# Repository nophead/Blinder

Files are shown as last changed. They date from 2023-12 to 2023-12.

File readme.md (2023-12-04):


# Blinder

Tasmota roller blind open / close mechanism

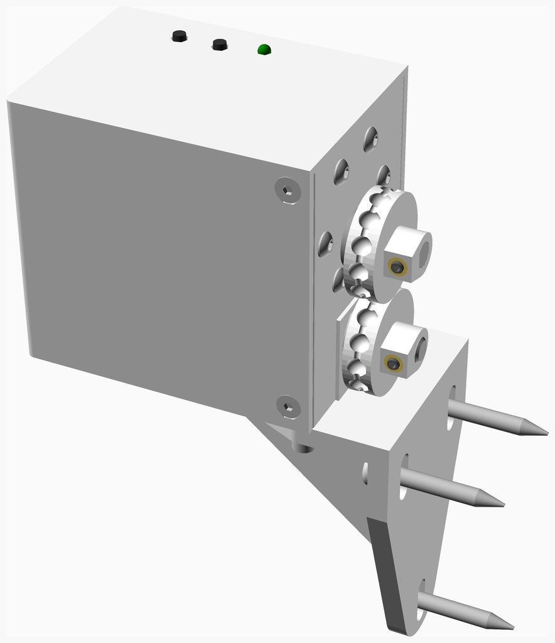
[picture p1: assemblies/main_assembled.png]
Main Assembly


<span></span>

---
## Table of Contents
1. [Parts list](#Parts_list)
1. [Pulley Assembly](#pulley_assembly)
1. [Switch Slide Assembly](#switch_slide_assembly)
1. [Rod Assembly](#rod_assembly)
1. [Retainer Assembly](#retainer_assembly)
1. [Idler Assembly](#idler_assembly)
1. [Base Assembly](#base_assembly)
1. [Motor Assembly](#motor_assembly)
1. [Bracket Assembly](#bracket_assembly)
1. [Blinder PCB Assembly](#blinder_PCB_assembly)
1. [Cover Assembly](#cover_assembly)
1. [Main Assembly](#main_assembly)

<span></span>
[Top](#TOP)

---

## Parts list
| <span style="writing-mode: vertical-rl; text-orientation: mixed;">Switch&nbsp;Slide</span> | <span style="writing-mode: vertical-rl; text-orientation: mixed;">Rod</span> | <span style="writing-mode: vertical-rl; text-orientation: mixed;">Base</span> | <span style="writing-mode: vertical-rl; text-orientation: mixed;">Motor</span> | <span style="writing-mode: vertical-rl; text-orientation: mixed;">Bracket</span> | <span style="writing-mode: vertical-rl; text-orientation: mixed;">Blinder&nbsp;PCB</span> | <span style="writing-mode: vertical-rl; text-orientation: mixed;">Cover</span> | <span style="writing-mode: vertical-rl; text-orientation: mixed;">Main</span> | <span style="writing-mode: vertical-rl; text-orientation: mixed;">TOTALS</span> |  |
|---:|---:|---:|---:|---:|---:|---:|---:|---:|:---|
|  |  |  |  |  |  |  |  | | **Vitamins** |
| &nbsp;&nbsp;.&nbsp; | &nbsp;&nbsp;.&nbsp; | &nbsp;&nbsp;2&nbsp; | &nbsp;&nbsp;.&nbsp; | &nbsp;&nbsp;.&nbsp; | &nbsp;&nbsp;.&nbsp; | &nbsp;&nbsp;.&nbsp; | &nbsp;&nbsp;.&nbsp; |  &nbsp;&nbsp;2&nbsp; | &nbsp;&nbsp; Ball bearing 686ZZ 6mm x 13mm x 5mm |
| &nbsp;&nbsp;.&nbsp; | &nbsp;&nbsp;.&nbsp; | &nbsp;&nbsp;.&nbsp; | &nbsp;&nbsp;.&nbsp; | &nbsp;&nbsp;.&nbsp; | &nbsp;&nbsp;1&nbsp; | &nbsp;&nbsp;.&nbsp; | &nbsp;&nbsp;.&nbsp; |  &nbsp;&nbsp;1&nbsp; | &nbsp;&nbsp; ESP-12F ESP8266 WiFi module |
| &nbsp;&nbsp;2&nbsp; | &nbsp;&nbsp;.&nbsp; | &nbsp;&nbsp;2&nbsp; | &nbsp;&nbsp;.&nbsp; | &nbsp;&nbsp;.&nbsp; | &nbsp;&nbsp;.&nbsp; | &nbsp;&nbsp;.&nbsp; | &nbsp;&nbsp;.&nbsp; |  &nbsp;&nbsp;4&nbsp; | &nbsp;&nbsp; Heatfit insert M2 x 4mm |
| &nbsp;&nbsp;.&nbsp; | &nbsp;&nbsp;.&nbsp; | &nbsp;&nbsp;10&nbsp; | &nbsp;&nbsp;1&nbsp; | &nbsp;&nbsp;.&nbsp; | &nbsp;&nbsp;.&nbsp; | &nbsp;&nbsp;.&nbsp; | &nbsp;&nbsp;.&nbsp; |  &nbsp;&nbsp;11&nbsp; | &nbsp;&nbsp; Heatfit insert M3 x 3mm |
| &nbsp;&nbsp;.&nbsp; | &nbsp;&nbsp;.&nbsp; | &nbsp;&nbsp;.&nbsp; | &nbsp;&nbsp;.&nbsp; | &nbsp;&nbsp;.&nbsp; | &nbsp;&nbsp;1&nbsp; | &nbsp;&nbsp;.&nbsp; | &nbsp;&nbsp;.&nbsp; |  &nbsp;&nbsp;1&nbsp; | &nbsp;&nbsp; JST PH connector 2 way |
| &nbsp;&nbsp;.&nbsp; | &nbsp;&nbsp;.&nbsp; | &nbsp;&nbsp;.&nbsp; | &nbsp;&nbsp;.&nbsp; | &nbsp;&nbsp;.&nbsp; | &nbsp;&nbsp;2&nbsp; | &nbsp;&nbsp;.&nbsp; | &nbsp;&nbsp;.&nbsp; |  &nbsp;&nbsp;2&nbsp; | &nbsp;&nbsp; JST PH connector 3 way |
| &nbsp;&nbsp;.&nbsp; | &nbsp;&nbsp;.&nbsp; | &nbsp;&nbsp;.&nbsp; | &nbsp;&nbsp;.&nbsp; | &nbsp;&nbsp;.&nbsp; | &nbsp;&nbsp;1&nbsp; | &nbsp;&nbsp;.&nbsp; | &nbsp;&nbsp;.&nbsp; |  &nbsp;&nbsp;1&nbsp; | &nbsp;&nbsp; LED 3 mm green |
| &nbsp;&nbsp;.&nbsp; | &nbsp;&nbsp;.&nbsp; | &nbsp;&nbsp;.&nbsp; | &nbsp;&nbsp;.&nbsp; | &nbsp;&nbsp;.&nbsp; | &nbsp;&nbsp;1&nbsp; | &nbsp;&nbsp;.&nbsp; | &nbsp;&nbsp;.&nbsp; |  &nbsp;&nbsp;1&nbsp; | &nbsp;&nbsp; MULTIWATT11 L6203 |
| &nbsp;&nbsp;1&nbsp; | &nbsp;&nbsp;.&nbsp; | &nbsp;&nbsp;1&nbsp; | &nbsp;&nbsp;.&nbsp; | &nbsp;&nbsp;.&nbsp; | &nbsp;&nbsp;.&nbsp; | &nbsp;&nbsp;.&nbsp; | &nbsp;&nbsp;.&nbsp; |  &nbsp;&nbsp;2&nbsp; | &nbsp;&nbsp; Microswitch DM1-00P-110-3 |
| &nbsp;&nbsp;.&nbsp; | &nbsp;&nbsp;.&nbsp; | &nbsp;&nbsp;.&nbsp; | &nbsp;&nbsp;.&nbsp; | &nbsp;&nbsp;.&nbsp; | &nbsp;&nbsp;1&nbsp; | &nbsp;&nbsp;.&nbsp; | &nbsp;&nbsp;.&nbsp; |  &nbsp;&nbsp;1&nbsp; | &nbsp;&nbsp; Molex KK header 2 way |
| &nbsp;&nbsp;.&nbsp; | &nbsp;&nbsp;.&nbsp; | &nbsp;&nbsp;.&nbsp; | &nbsp;&nbsp;.&nbsp; | &nbsp;&nbsp;.&nbsp; | &nbsp;&nbsp;1&nbsp; | &nbsp;&nbsp;.&nbsp; | &nbsp;&nbsp;.&nbsp; |  &nbsp;&nbsp;1&nbsp; | &nbsp;&nbsp; Molex KK housing 2 way |
| &nbsp;&nbsp;.&nbsp; | &nbsp;&nbsp;.&nbsp; | &nbsp;&nbsp;.&nbsp; | &nbsp;&nbsp;.&nbsp; | &nbsp;&nbsp;.&nbsp; | &nbsp;&nbsp;.&nbsp; | &nbsp;&nbsp;1&nbsp; | &nbsp;&nbsp;.&nbsp; |  &nbsp;&nbsp;1&nbsp; | &nbsp;&nbsp; Nut M3 x 2.4mm nyloc |
| &nbsp;&nbsp;.&nbsp; | &nbsp;&nbsp;.&nbsp; | &nbsp;&nbsp;1&nbsp; | &nbsp;&nbsp;.&nbsp; | &nbsp;&nbsp;.&nbsp; | &nbsp;&nbsp;.&nbsp; | &nbsp;&nbsp;.&nbsp; | &nbsp;&nbsp;.&nbsp; |  &nbsp;&nbsp;1&nbsp; | &nbsp;&nbsp; Nut M8 x 6.5mm brass |
| &nbsp;&nbsp;.&nbsp; | &nbsp;&nbsp;.&nbsp; | &nbsp;&nbsp;.&nbsp; | &nbsp;&nbsp;.&nbsp; | &nbsp;&nbsp;.&nbsp; | &nbsp;&nbsp;1&nbsp; | &nbsp;&nbsp;.&nbsp; | &nbsp;&nbsp;.&nbsp; |  &nbsp;&nbsp;1&nbsp; | &nbsp;&nbsp; PCB Blinder |
| &nbsp;&nbsp;.&nbsp; | &nbsp;&nbsp;.&nbsp; | &nbsp;&nbsp;.&nbsp; | &nbsp;&nbsp;.&nbsp; | &nbsp;&nbsp;.&nbsp; | &nbsp;&nbsp;2&nbsp; | &nbsp;&nbsp;.&nbsp; | &nbsp;&nbsp;.&nbsp; |  &nbsp;&nbsp;2&nbsp; | &nbsp;&nbsp; SMD capacitor 0805 100n |
| &nbsp;&nbsp;.&nbsp; | &nbsp;&nbsp;.&nbsp; | &nbsp;&nbsp;.&nbsp; | &nbsp;&nbsp;.&nbsp; | &nbsp;&nbsp;.&nbsp; | &nbsp;&nbsp;2&nbsp; | &nbsp;&nbsp;.&nbsp; | &nbsp;&nbsp;.&nbsp; |  &nbsp;&nbsp;2&nbsp; | &nbsp;&nbsp; SMD capacitor 0805 15n |
| &nbsp;&nbsp;.&nbsp; | &nbsp;&nbsp;.&nbsp; | &nbsp;&nbsp;.&nbsp; | &nbsp;&nbsp;.&nbsp; | &nbsp;&nbsp;.&nbsp; | &nbsp;&nbsp;1&nbsp; | &nbsp;&nbsp;.&nbsp; | &nbsp;&nbsp;.&nbsp; |  &nbsp;&nbsp;1&nbsp; | &nbsp;&nbsp; SMD capacitor 0805 220n |
| &nbsp;&nbsp;.&nbsp; | &nbsp;&nbsp;.&nbsp; | &nbsp;&nbsp;.&nbsp; | &nbsp;&nbsp;.&nbsp; | &nbsp;&nbsp;.&nbsp; | &nbsp;&nbsp;5&nbsp; | &nbsp;&nbsp;.&nbsp; | &nbsp;&nbsp;.&nbsp; |  &nbsp;&nbsp;5&nbsp; | &nbsp;&nbsp; SMD resistor 0805 10K 0.125W |
| &nbsp;&nbsp;.&nbsp; | &nbsp;&nbsp;.&nbsp; | &nbsp;&nbsp;.&nbsp; | &nbsp;&nbsp;.&nbsp; | &nbsp;&nbsp;.&nbsp; | &nbsp;&nbsp;2&nbsp; | &nbsp;&nbsp;.&nbsp; | &nbsp;&nbsp;.&nbsp; |  &nbsp;&nbsp;2&nbsp; | &nbsp;&nbsp; SMD resistor 0805 1K 0.125W |
| &nbsp;&nbsp;.&nbsp; | &nbsp;&nbsp;.&nbsp; | &nbsp;&nbsp;.&nbsp; | &nbsp;&nbsp;.&nbsp; | &nbsp;&nbsp;.&nbsp; | &nbsp;&nbsp;1&nbsp; | &nbsp;&nbsp;.&nbsp; | &nbsp;&nbsp;.&nbsp; |  &nbsp;&nbsp;1&nbsp; | &nbsp;&nbsp; SMD resistor 0805 2K2 0.125W |
| &nbsp;&nbsp;2&nbsp; | &nbsp;&nbsp;.&nbsp; | &nbsp;&nbsp;2&nbsp; | &nbsp;&nbsp;.&nbsp; | &nbsp;&nbsp;.&nbsp; | &nbsp;&nbsp;.&nbsp; | &nbsp;&nbsp;.&nbsp; | &nbsp;&nbsp;.&nbsp; |  &nbsp;&nbsp;4&nbsp; | &nbsp;&nbsp; Screw M2 cap x 10mm |
| &nbsp;&nbsp;.&nbsp; | &nbsp;&nbsp;.&nbsp; | &nbsp;&nbsp;1&nbsp; | &nbsp;&nbsp;.&nbsp; | &nbsp;&nbsp;.&nbsp; | &nbsp;&nbsp;.&nbsp; | &nbsp;&nbsp;.&nbsp; | &nbsp;&nbsp;.&nbsp; |  &nbsp;&nbsp;1&nbsp; | &nbsp;&nbsp; Screw M3 cap x  5mm |
| &nbsp;&nbsp;.&nbsp; | &nbsp;&nbsp;.&nbsp; | &nbsp;&nbsp;.&nbsp; | &nbsp;&nbsp;.&nbsp; | &nbsp;&nbsp;3&nbsp; | &nbsp;&nbsp;.&nbsp; | &nbsp;&nbsp;.&nbsp; | &nbsp;&nbsp;.&nbsp; |  &nbsp;&nbsp;3&nbsp; | &nbsp;&nbsp; Screw M3 cap x  8mm |
| &nbsp;&nbsp;.&nbsp; | &nbsp;&nbsp;.&nbsp; | &nbsp;&nbsp;.&nbsp; | &nbsp;&nbsp;.&nbsp; | &nbsp;&nbsp;.&nbsp; | &nbsp;&nbsp;.&nbsp; | &nbsp;&nbsp;.&nbsp; | &nbsp;&nbsp;4&nbsp; |  &nbsp;&nbsp;4&nbsp; | &nbsp;&nbsp; Screw M3 cs cap x  5mm |
| &nbsp;&nbsp;.&nbsp; | &nbsp;&nbsp;.&nbsp; | &nbsp;&nbsp;.&nbsp; | &nbsp;&nbsp;.&nbsp; | &nbsp;&nbsp;.&nbsp; | &nbsp;&nbsp;.&nbsp; | &nbsp;&nbsp;1&nbsp; | &nbsp;&nbsp;.&nbsp; |  &nbsp;&nbsp;1&nbsp; | &nbsp;&nbsp; Screw M3 cs cap x 12mm |
| &nbsp;&nbsp;.&nbsp; | &nbsp;&nbsp;.&nbsp; | &nbsp;&nbsp;.&nbsp; | &nbsp;&nbsp;6&nbsp; | &nbsp;&nbsp;.&nbsp; | &nbsp;&nbsp;.&nbsp; | &nbsp;&nbsp;.&nbsp; | &nbsp;&nbsp;.&nbsp; |  &nbsp;&nbsp;6&nbsp; | &nbsp;&nbsp; Screw M3 dome x 12mm |
| &nbsp;&nbsp;.&nbsp; | &nbsp;&nbsp;.&nbsp; | &nbsp;&nbsp;2&nbsp; | &nbsp;&nbsp;1&nbsp; | &nbsp;&nbsp;.&nbsp; | &nbsp;&nbsp;.&nbsp; | &nbsp;&nbsp;.&nbsp; | &nbsp;&nbsp;.&nbsp; |  &nbsp;&nbsp;3&nbsp; | &nbsp;&nbsp; Screw M3 grub x  5mm |
| &nbsp;&nbsp;.&nbsp; | &nbsp;&nbsp;.&nbsp; | &nbsp;&nbsp;.&nbsp; | &nbsp;&nbsp;.&nbsp; | &nbsp;&nbsp;3&nbsp; | &nbsp;&nbsp;.&nbsp; | &nbsp;&nbsp;.&nbsp; | &nbsp;&nbsp;.&nbsp; |  &nbsp;&nbsp;3&nbsp; | &nbsp;&nbsp; Screw No8 pan wood x 30mm |
| &nbsp;&nbsp;.&nbsp; | &nbsp;&nbsp;.&nbsp; | &nbsp;&nbsp;.&nbsp; | &nbsp;&nbsp;.&nbsp; | &nbsp;&nbsp;.&nbsp; | &nbsp;&nbsp;2&nbsp; | &nbsp;&nbsp;.&nbsp; | &nbsp;&nbsp;.&nbsp; |  &nbsp;&nbsp;2&nbsp; | &nbsp;&nbsp; Square button 6mm |
| &nbsp;&nbsp;.&nbsp; | &nbsp;&nbsp;1&nbsp; | &nbsp;&nbsp;.&nbsp; | &nbsp;&nbsp;.&nbsp; | &nbsp;&nbsp;.&nbsp; | &nbsp;&nbsp;.&nbsp; | &nbsp;&nbsp;.&nbsp; | &nbsp;&nbsp;.&nbsp; |  &nbsp;&nbsp;1&nbsp; | &nbsp;&nbsp; Threaded rod M8 x 79mm - not shown |
| &nbsp;&nbsp;.&nbsp; | &nbsp;&nbsp;.&nbsp; | &nbsp;&nbsp;.&nbsp; | &nbsp;&nbsp;.&nbsp; | &nbsp;&nbsp;.&nbsp; | &nbsp;&nbsp;1&nbsp; | &nbsp;&nbsp;.&nbsp; | &nbsp;&nbsp;.&nbsp; |  &nbsp;&nbsp;1&nbsp; | &nbsp;&nbsp; Ultra Small 3A buck regulator |
| &nbsp;&nbsp;2&nbsp; | &nbsp;&nbsp;.&nbsp; | &nbsp;&nbsp;2&nbsp; | &nbsp;&nbsp;.&nbsp; | &nbsp;&nbsp;.&nbsp; | &nbsp;&nbsp;.&nbsp; | &nbsp;&nbsp;.&nbsp; | &nbsp;&nbsp;.&nbsp; |  &nbsp;&nbsp;4&nbsp; | &nbsp;&nbsp; Washer  M2 x 5mm x 0.3mm |
| &nbsp;&nbsp;.&nbsp; | &nbsp;&nbsp;.&nbsp; | &nbsp;&nbsp;1&nbsp; | &nbsp;&nbsp;.&nbsp; | &nbsp;&nbsp;3&nbsp; | &nbsp;&nbsp;.&nbsp; | &nbsp;&nbsp;1&nbsp; | &nbsp;&nbsp;.&nbsp; |  &nbsp;&nbsp;5&nbsp; | &nbsp;&nbsp; Washer  M3 x 7mm x 0.5mm |
| &nbsp;&nbsp;.&nbsp; | &nbsp;&nbsp;.&nbsp; | &nbsp;&nbsp;.&nbsp; | &nbsp;&nbsp;.&nbsp; | &nbsp;&nbsp;3&nbsp; | &nbsp;&nbsp;.&nbsp; | &nbsp;&nbsp;.&nbsp; | &nbsp;&nbsp;.&nbsp; |  &nbsp;&nbsp;3&nbsp; | &nbsp;&nbsp; Washer  M5 x 10mm x 1mm |
| &nbsp;&nbsp;.&nbsp; | &nbsp;&nbsp;.&nbsp; | &nbsp;&nbsp;2&nbsp; | &nbsp;&nbsp;.&nbsp; | &nbsp;&nbsp;.&nbsp; | &nbsp;&nbsp;.&nbsp; | &nbsp;&nbsp;.&nbsp; | &nbsp;&nbsp;.&nbsp; |  &nbsp;&nbsp;2&nbsp; | &nbsp;&nbsp; Washer spring M6 x 1.9mm |
| &nbsp;&nbsp;2&nbsp; | &nbsp;&nbsp;.&nbsp; | &nbsp;&nbsp;2&nbsp; | &nbsp;&nbsp;.&nbsp; | &nbsp;&nbsp;.&nbsp; | &nbsp;&nbsp;.&nbsp; | &nbsp;&nbsp;.&nbsp; | &nbsp;&nbsp;.&nbsp; |  &nbsp;&nbsp;4&nbsp; | &nbsp;&nbsp; Washer star M2 x 0.3mm |
| &nbsp;&nbsp;.&nbsp; | &nbsp;&nbsp;.&nbsp; | &nbsp;&nbsp;1&nbsp; | &nbsp;&nbsp;.&nbsp; | &nbsp;&nbsp;.&nbsp; | &nbsp;&nbsp;.&nbsp; | &nbsp;&nbsp;.&nbsp; | &nbsp;&nbsp;.&nbsp; |  &nbsp;&nbsp;1&nbsp; | &nbsp;&nbsp; Washer star M3 x 0.5mm |
| &nbsp;&nbsp;9&nbsp; | &nbsp;&nbsp;1&nbsp; | &nbsp;&nbsp;29&nbsp; | &nbsp;&nbsp;8&nbsp; | &nbsp;&nbsp;12&nbsp; | &nbsp;&nbsp;25&nbsp; | &nbsp;&nbsp;3&nbsp; | &nbsp;&nbsp;4&nbsp; | &nbsp;&nbsp;91&nbsp; | &nbsp;&nbsp;Total vitamins count |
|  |  |  |  |  |  |  |  | | **3D printed parts** |
| &nbsp;&nbsp;.&nbsp; | &nbsp;&nbsp;.&nbsp; | &nbsp;&nbsp;1&nbsp; | &nbsp;&nbsp;.&nbsp; | &nbsp;&nbsp;.&nbsp; | &nbsp;&nbsp;.&nbsp; | &nbsp;&nbsp;.&nbsp; | &nbsp;&nbsp;.&nbsp; |  &nbsp;&nbsp;1&nbsp; | &nbsp;&nbsp;base.stl |
| &nbsp;&nbsp;.&nbsp; | &nbsp;&nbsp;.&nbsp; | &nbsp;&nbsp;.&nbsp; | &nbsp;&nbsp;.&nbsp; | &nbsp;&nbsp;1&nbsp; | &nbsp;&nbsp;.&nbsp; | &nbsp;&nbsp;.&nbsp; | &nbsp;&nbsp;.&nbsp; |  &nbsp;&nbsp;1&nbsp; | &nbsp;&nbsp;bracket.stl |
| &nbsp;&nbsp;.&nbsp; | &nbsp;&nbsp;.&nbsp; | &nbsp;&nbsp;.&nbsp; | &nbsp;&nbsp;.&nbsp; | &nbsp;&nbsp;.&nbsp; | &nbsp;&nbsp;.&nbsp; | &nbsp;&nbsp;1&nbsp; | &nbsp;&nbsp;.&nbsp; |  &nbsp;&nbsp;1&nbsp; | &nbsp;&nbsp;cover.stl |
| &nbsp;&nbsp;.&nbsp; | &nbsp;&nbsp;.&nbsp; | &nbsp;&nbsp;1&nbsp; | &nbsp;&nbsp;.&nbsp; | &nbsp;&nbsp;.&nbsp; | &nbsp;&nbsp;.&nbsp; | &nbsp;&nbsp;.&nbsp; | &nbsp;&nbsp;.&nbsp; |  &nbsp;&nbsp;1&nbsp; | &nbsp;&nbsp;idler.stl |
| &nbsp;&nbsp;.&nbsp; | &nbsp;&nbsp;.&nbsp; | &nbsp;&nbsp;.&nbsp; | &nbsp;&nbsp;1&nbsp; | &nbsp;&nbsp;.&nbsp; | &nbsp;&nbsp;.&nbsp; | &nbsp;&nbsp;.&nbsp; | &nbsp;&nbsp;.&nbsp; |  &nbsp;&nbsp;1&nbsp; | &nbsp;&nbsp;pulley.stl |
| &nbsp;&nbsp;.&nbsp; | &nbsp;&nbsp;.&nbsp; | &nbsp;&nbsp;1&nbsp; | &nbsp;&nbsp;.&nbsp; | &nbsp;&nbsp;.&nbsp; | &nbsp;&nbsp;.&nbsp; | &nbsp;&nbsp;.&nbsp; | &nbsp;&nbsp;.&nbsp; |  &nbsp;&nbsp;1&nbsp; | &nbsp;&nbsp;retainer.stl |
| &nbsp;&nbsp;1&nbsp; | &nbsp;&nbsp;.&nbsp; | &nbsp;&nbsp;.&nbsp; | &nbsp;&nbsp;.&nbsp; | &nbsp;&nbsp;.&nbsp; | &nbsp;&nbsp;.&nbsp; | &nbsp;&nbsp;.&nbsp; | &nbsp;&nbsp;.&nbsp; |  &nbsp;&nbsp;1&nbsp; | &nbsp;&nbsp;switch_slide.stl |
| &nbsp;&nbsp;1&nbsp; | &nbsp;&nbsp;.&nbsp; | &nbsp;&nbsp;3&nbsp; | &nbsp;&nbsp;1&nbsp; | &nbsp;&nbsp;1&nbsp; | &nbsp;&nbsp;.&nbsp; | &nbsp;&nbsp;1&nbsp; | &nbsp;&nbsp;.&nbsp; | &nbsp;&nbsp;7&nbsp; | &nbsp;&nbsp;Total 3D printed parts count |

<span></span>
[Top](#TOP)

---

## Pulley Assembly
### Vitamins
|Qty|Description|
|---:|:---|
|1| Heatfit insert M3 x 3mm|
|1| Screw M3 grub x  5mm|

### 3D Printed parts

| 1 x pulley.stl |
|---|
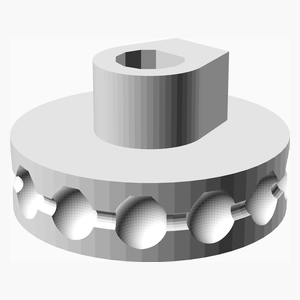
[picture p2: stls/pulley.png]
pulley.stl
|  

### Assembly instructions
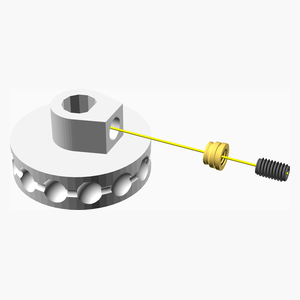
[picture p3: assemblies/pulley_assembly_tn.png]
pulley_assembly


1. Fit the heatfit insert
1. Add the grub screw

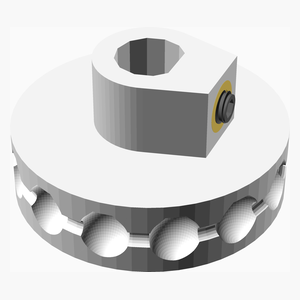
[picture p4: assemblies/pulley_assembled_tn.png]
pulley_assembled


<span></span>
[Top](#TOP)

---

## Switch Slide Assembly
### Vitamins
|Qty|Description|
|---:|:---|
|2| Heatfit insert M2 x 4mm|
|1| Microswitch DM1-00P-110-3|
|2| Screw M2 cap x 10mm|
|2| Washer  M2 x 5mm x 0.3mm|
|2| Washer star M2 x 0.3mm|

### 3D Printed parts

| 1 x switch_slide.stl |
|---|
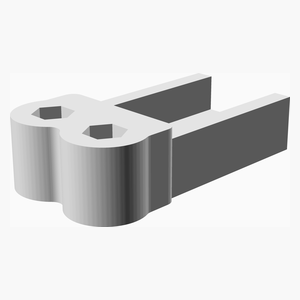
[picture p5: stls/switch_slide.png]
switch_slide.stl
|  

### Assembly instructions
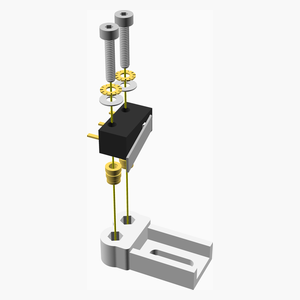
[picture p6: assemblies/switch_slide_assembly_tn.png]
switch_slide_assembly


1. Fit the heatfit inserts into the slide.
1. Screw the microswitch to the slide using 10mm M2 cap screws spring washers and plain washers.
1. Solder two wires to the outer pins.

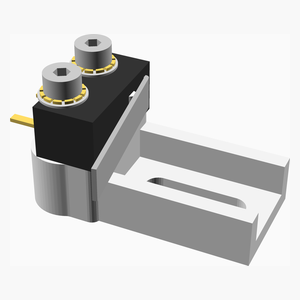
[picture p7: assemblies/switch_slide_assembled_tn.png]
switch_slide_assembled


<span></span>
[Top](#TOP)

---

## Rod Assembly
### Vitamins
|Qty|Description|
|---:|:---|
|1| Threaded rod M8 x 79mm - not shown|

### Assembly instructions
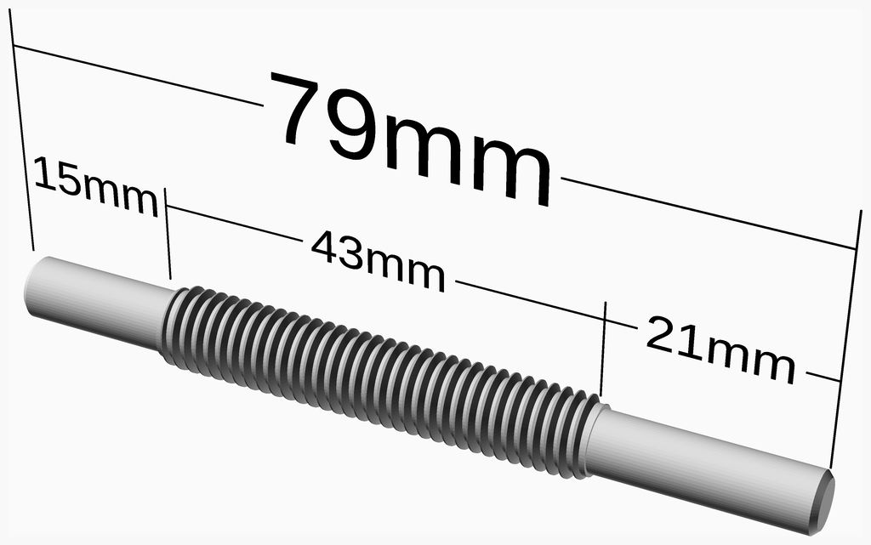
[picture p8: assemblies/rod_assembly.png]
rod_assembly


* Turn down the ends of the studding to 5.96mm to fit through the bearings.

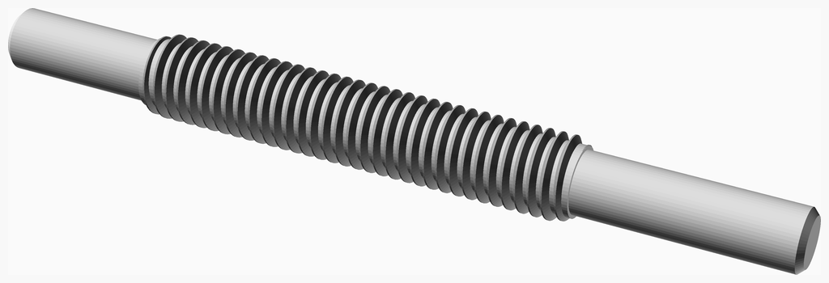
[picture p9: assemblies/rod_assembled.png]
rod_assembled


<span></span>
[Top](#TOP)

---

## Retainer Assembly
### Vitamins
|Qty|Description|
|---:|:---|
|1| Heatfit insert M3 x 3mm|
|1| Screw M3 grub x  5mm|

### 3D Printed parts

| 1 x retainer.stl |
|---|
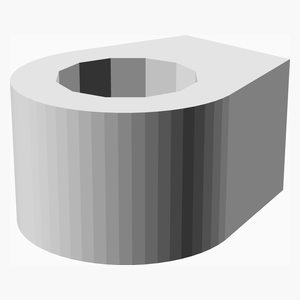
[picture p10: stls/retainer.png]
retainer.stl
|  

### Assembly instructions
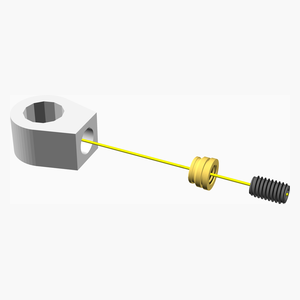
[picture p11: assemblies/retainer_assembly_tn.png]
retainer_assembly


1. Fit the heatfit insert
1. Add the grub screw

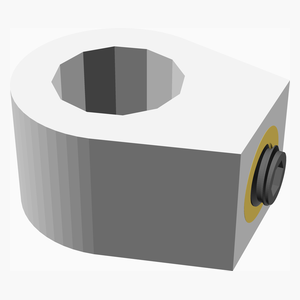
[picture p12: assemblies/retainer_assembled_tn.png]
retainer_assembled


<span></span>
[Top](#TOP)

---

## Idler Assembly
### Vitamins
|Qty|Description|
|---:|:---|
|1| Heatfit insert M3 x 3mm|
|1| Screw M3 grub x  5mm|

### 3D Printed parts

| 1 x idler.stl |
|---|
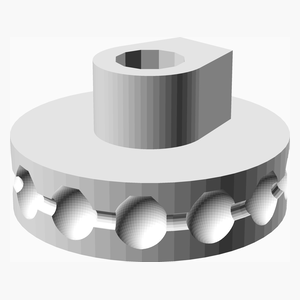
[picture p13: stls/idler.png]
idler.stl
|  

### Assembly instructions
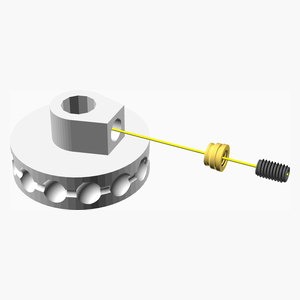
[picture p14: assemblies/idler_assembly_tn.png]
idler_assembly


1. Fit the heatfit insert
1. Add the grub screw

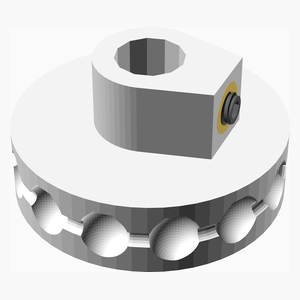
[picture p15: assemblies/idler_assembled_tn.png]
idler_assembled


<span></span>
[Top](#TOP)

---

## Base Assembly
### Vitamins
|Qty|Description|
|---:|:---|
|2| Ball bearing 686ZZ 6mm x 13mm x 5mm|
|2| Heatfit insert M2 x 4mm|
|8| Heatfit insert M3 x 3mm|
|1| Microswitch DM1-00P-110-3|
|1| Nut M8 x 6.5mm brass|
|2| Screw M2 cap x 10mm|
|1| Screw M3 cap x  5mm|
|2| Washer  M2 x 5mm x 0.3mm|
|1| Washer  M3 x 7mm x 0.5mm|
|2| Washer spring M6 x 1.9mm|
|2| Washer star M2 x 0.3mm|
|1| Washer star M3 x 0.5mm|

### 3D Printed parts

| 1 x base.stl |
|---|
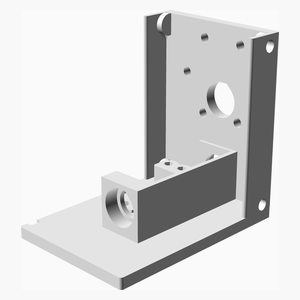
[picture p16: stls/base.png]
base.stl
|  

### Sub-assemblies

| 1 x idler_assembly | 1 x retainer_assembly | 1 x rod_assembly |
|---|---|---|
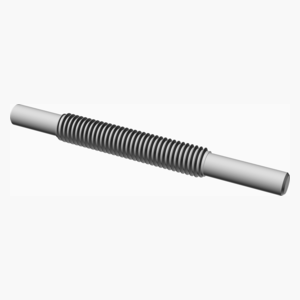
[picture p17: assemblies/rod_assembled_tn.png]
rod_assembled
| idler_assembled | retainer_assembled |  

| 1 x switch_slide_assembly |
|---|
| switch_slide_assembled 

### Assembly instructions
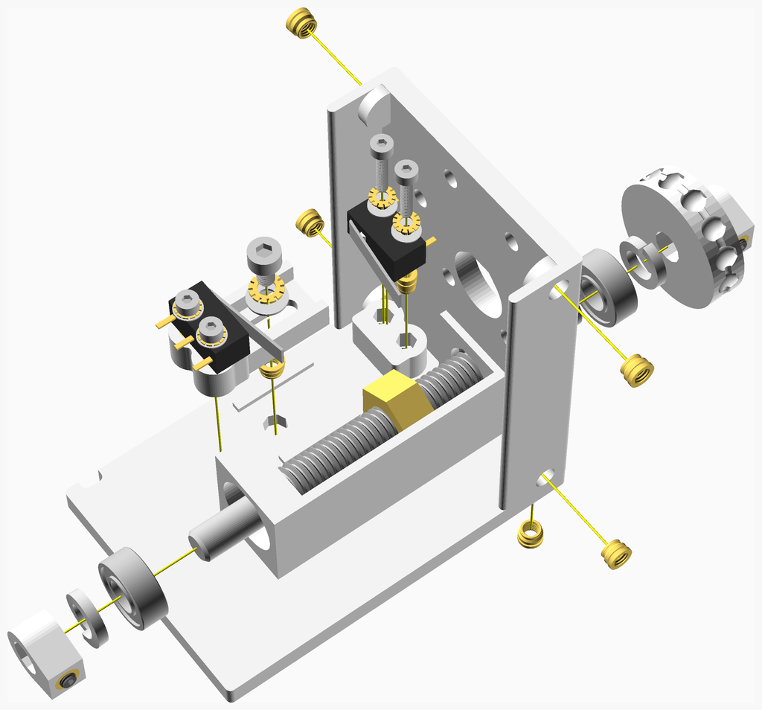
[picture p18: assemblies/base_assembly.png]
base_assembly


1. Fit the 8 M3 inserts, 4 in the ribs, 3 in the base and 1 for the slide
1. Fit two M2 inserts for the microswitch.
1. Place the M8 nut in a central position and screw in the studding.
1. Crush the M8 spring washers with pliers as they are used just as spacers.
1. Fit the bearings and spring washers and secure in place with the pulley and retainer grub screws.
1. Solder two wires to the outer pins of the microswitch and screw it in place.
1. Screw the slide in place in the central position.

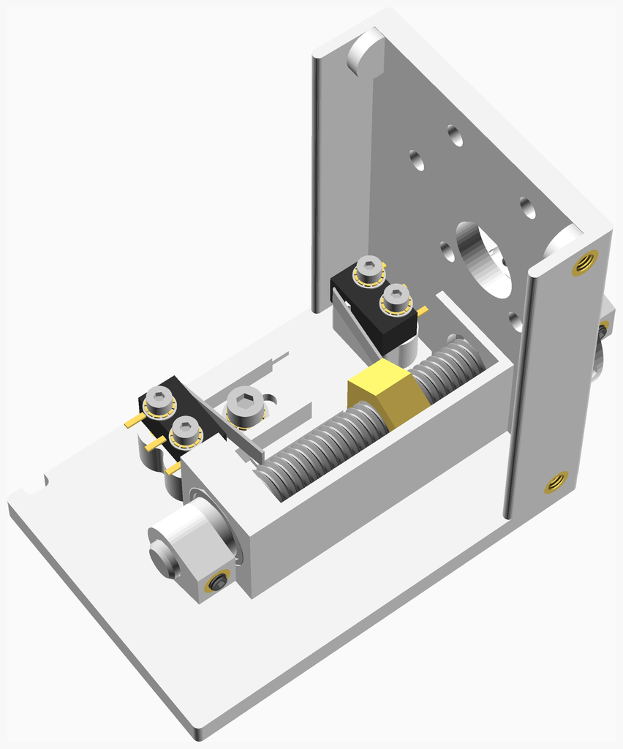
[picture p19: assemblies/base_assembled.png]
base_assembled


<span></span>
[Top](#TOP)

---

## Motor Assembly
### Vitamins
|Qty|Description|
|---:|:---|
|6| Screw M3 dome x 12mm|

### Sub-assemblies

| 1 x base_assembly | 1 x pulley_assembly |
|---|---|
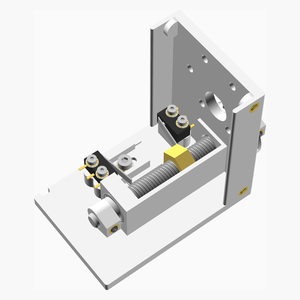
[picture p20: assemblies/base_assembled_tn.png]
base_assembled
|  | pulley_assembled 

### Assembly instructions
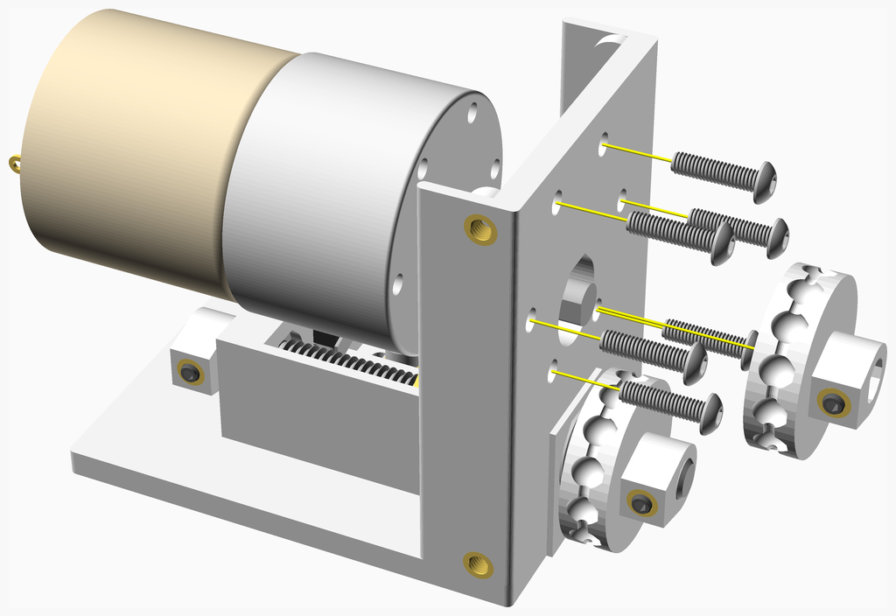
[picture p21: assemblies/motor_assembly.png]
motor_assembly


1. Introduce the motor and pulley trapping the ball chain between the pulley and the idler and then screw the motor in place.
1. Solder wires to the motor.
1. Crimp JST plugs to the motors and switch wires. Use the schematic to get the correct pins.

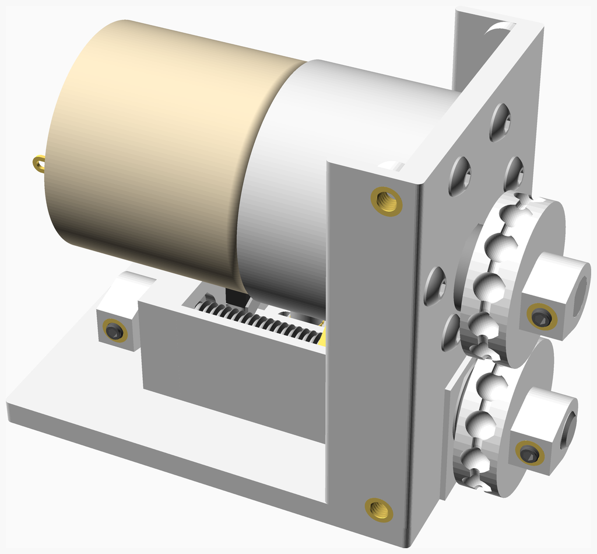
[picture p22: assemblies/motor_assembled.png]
motor_assembled


<span></span>
[Top](#TOP)

---

## Bracket Assembly
### Vitamins
|Qty|Description|
|---:|:---|
|3| Screw M3 cap x  8mm|
|3| Screw No8 pan wood x 30mm|
|3| Washer  M3 x 7mm x 0.5mm|
|3| Washer  M5 x 10mm x 1mm|

### 3D Printed parts

| 1 x bracket.stl |
|---|
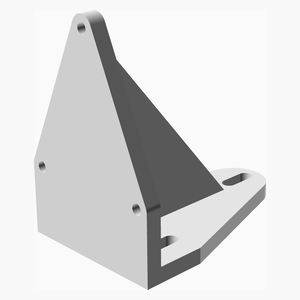
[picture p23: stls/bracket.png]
bracket.stl
|  

### Sub-assemblies

| 1 x motor_assembly |
|---|
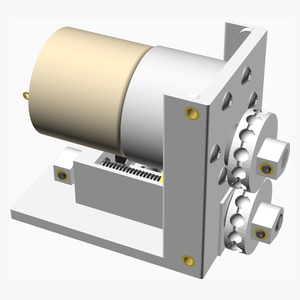
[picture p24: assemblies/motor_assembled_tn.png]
motor_assembled
|  

### Assembly instructions
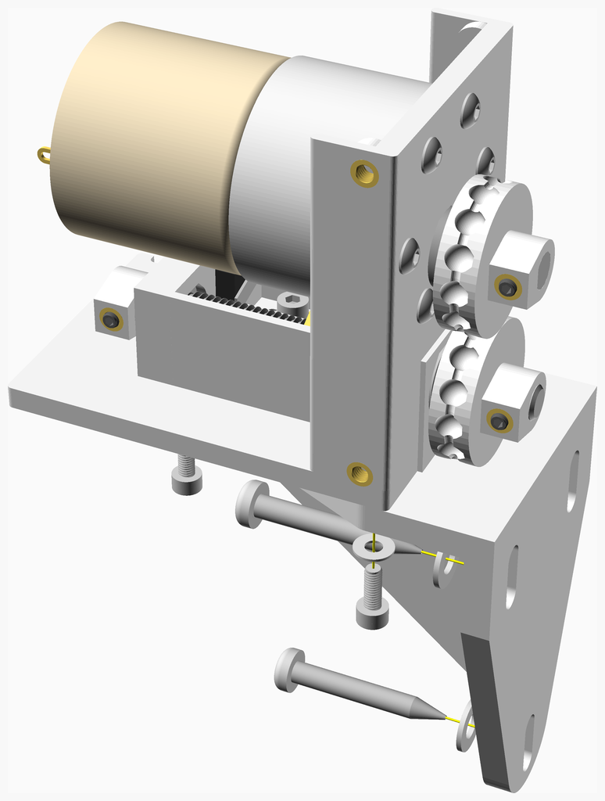
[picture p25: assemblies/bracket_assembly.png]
bracket_assembly


1. Screw the bracket to the bottom of the base using 3 8mm M3 cap screws and washers.
1. Screw the bracket to the wall using rawl plugs, No8 screws and M5 washers.
1. Slide it down to tension the ball chain before tightening the screws.
1. Connect the PCB to the switches, motor and 12V power.
1. While controlling the blind with the buttons: adjust the closed position by losening the idler pulley and rotating it on the shaft.
1. Then set the open position by adjustinge the sliding microswitch.

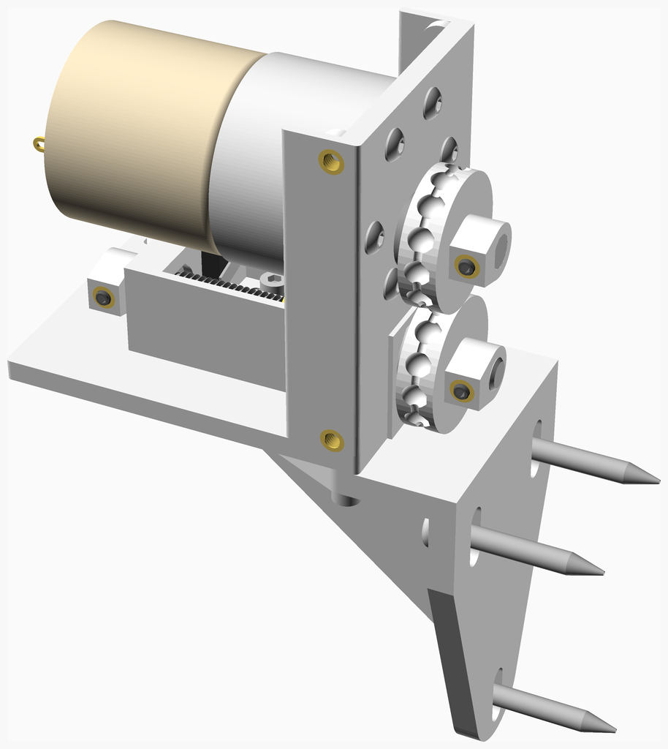
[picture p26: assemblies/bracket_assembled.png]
bracket_assembled


<span></span>
[Top](#TOP)

---

## Blinder PCB Assembly
### Vitamins
|Qty|Description|
|---:|:---|
|1| ESP-12F ESP8266 WiFi module|
|1| JST PH connector 2 way|
|2| JST PH connector 3 way|
|1| LED 3 mm green|
|1| MULTIWATT11 L6203|
|1| Molex KK header 2 way|
|1| Molex KK housing 2 way|
|1| PCB Blinder|
|2| SMD capacitor 0805 100n|
|2| SMD capacitor 0805 15n|
|1| SMD capacitor 0805 220n|
|5| SMD resistor 0805 10K 0.125W|
|2| SMD resistor 0805 1K 0.125W|
|1| SMD resistor 0805 2K2 0.125W|
|2| Square button 6mm|
|1| Ultra Small 3A buck regulator|

### Assembly instructions
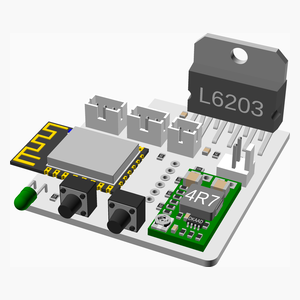
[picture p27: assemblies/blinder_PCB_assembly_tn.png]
blinder_PCB_assembly


1. Use a paste mask to apply solder paste to the SMD pads.
1. Place the SMD parts on the solder.
1. Use an oven or hotplate to reflow the solder.
1. Alternatively the SMD parts and pads are big enough to hand solder.
1. Hand solder the through hole connectors, switches, LED and L6203. The LED's flange should align with the board edge.
1. Solder wires into the tink_buck converter, mount it on a double sided sticky pad and solder the wires to the PCB.
1. Crop all the leads short on the underside of the board.

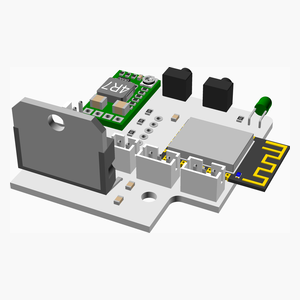
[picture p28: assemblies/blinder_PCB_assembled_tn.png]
blinder_PCB_assembled


<span></span>
[Top](#TOP)

---

## Cover Assembly
### Vitamins
|Qty|Description|
|---:|:---|
|1| Nut M3 x 2.4mm nyloc|
|1| Screw M3 cs cap x 12mm|
|1| Washer  M3 x 7mm x 0.5mm|

### 3D Printed parts

| 1 x cover.stl |
|---|
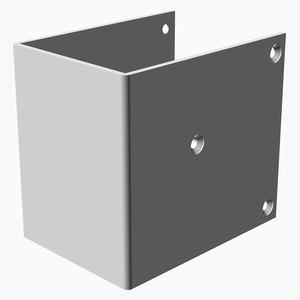
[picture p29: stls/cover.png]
cover.stl
|  

### Sub-assemblies

| 1 x blinder_PCB_assembly |
|---|
| blinder_PCB_assembled 

### Assembly instructions
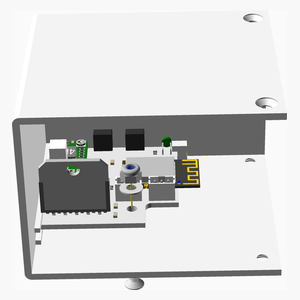
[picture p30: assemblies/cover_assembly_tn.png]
cover_assembly


1. Cut away the support material under the PCB spacer boss.
1. Place the PCB into the large guide and level with the top of the small guide and then slide forwards.
1. Secure with the screw, washer and nut.

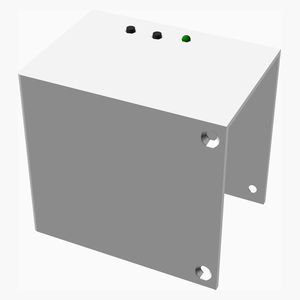
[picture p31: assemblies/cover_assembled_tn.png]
cover_assembled


<span></span>
[Top](#TOP)

---

## Main Assembly
### Vitamins
|Qty|Description|
|---:|:---|
|4| Screw M3 cs cap x  5mm|

### Sub-assemblies

| 1 x bracket_assembly | 1 x cover_assembly |
|---|---|
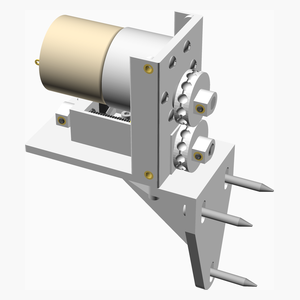
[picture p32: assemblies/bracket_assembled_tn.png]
bracket_assembled
|  | cover_assembled 

### Assembly instructions
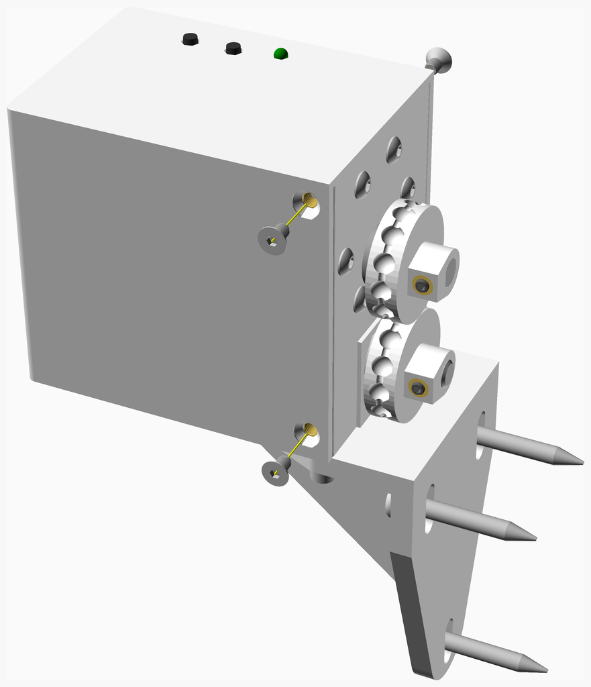
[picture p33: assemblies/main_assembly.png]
main_assembly


1. Place the 12V power cable in the slot in the base.
1. Place the cover assembly over the base and secure with four screws.

main_assembled

<span></span>
[Top](#TOP)

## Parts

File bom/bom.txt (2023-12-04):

Vitamins:
                               S
    B                          w
    l                          i
    i                          t
    n                    R     c
    d  B                 e     h
    e  r              P  t      
    r  a  C  I     M  u  a     s
 B     c  o  d  M  o  l  i     l
 a  p  k  v  l  a  t  l  n  R  i
 s  c  e  e  e  i  o  e  e  o  d
 e  b  t  r  r  n  r  y  r  d  e
 2|  |  |  |  |  |  |  |  |  |  |  2 Ball bearing 686ZZ 6mm x 13mm x 5mm
 8|  |  |  | 1|  |  | 1| 1|  |  | 11 Heatfit insert M3 x 3mm
 2|  |  |  |  |  |  |  |  |  | 2|  4 Heatfit insert M2 x 4mm
  | 1|  |  |  |  |  |  |  |  |  |  1 JST PH connector 2 way
  | 2|  |  |  |  |  |  |  |  |  |  2 JST PH connector 3 way
  | 1|  |  |  |  |  |  |  |  |  |  1 LED 3 mm green
 1|  |  |  |  |  |  |  |  |  | 1|  2 Microswitch DM1-00P-110-3
  | 1|  |  |  |  |  |  |  |  |  |  1 Molex KK header 2 way
  | 1|  |  |  |  |  |  |  |  |  |  1 Molex KK housing 2 way
  | 1|  |  |  |  |  |  |  |  |  |  1 MULTIWATT11 L6203
  |  |  | 1|  |  |  |  |  |  |  |  1 Nut M3 x 2.4mm nyloc
 1|  |  |  |  |  |  |  |  |  |  |  1 Nut M8 x 6.5mm brass
  | 1|  |  |  |  |  |  |  |  |  |  1 PCB Blinder
  | 1|  |  |  |  |  |  |  |  |  |  1 ESP-12F ESP8266 WiFi module
  | 1|  |  |  |  |  |  |  |  |  |  1 Ultra Small 3A buck regulator
 2|  |  |  |  |  |  |  |  |  | 2|  4 Screw M2 cap x 10mm
 1|  |  |  |  |  |  |  |  |  |  |  1 Screw M3 cap x  5mm
  |  | 3|  |  |  |  |  |  |  |  |  3 Screw M3 cap x  8mm
  |  |  | 1|  |  |  |  |  |  |  |  1 Screw M3 cs cap x 12mm
  |  |  |  |  | 4|  |  |  |  |  |  4 Screw M3 cs cap x  5mm
  |  |  |  |  |  | 6|  |  |  |  |  6 Screw M3 dome x 12mm
  |  |  |  | 1|  |  | 1| 1|  |  |  3 Screw M3 grub x  5mm
  |  | 3|  |  |  |  |  |  |  |  |  3 Screw No8 pan wood x 30mm
  | 2|  |  |  |  |  |  |  |  |  |  2 SMD capacitor 0805 100n
  | 2|  |  |  |  |  |  |  |  |  |  2 SMD capacitor 0805 15n
  | 1|  |  |  |  |  |  |  |  |  |  1 SMD capacitor 0805 220n
  | 5|  |  |  |  |  |  |  |  |  |  5 SMD resistor 0805 10K 0.125W
  | 2|  |  |  |  |  |  |  |  |  |  2 SMD resistor 0805 1K 0.125W
  | 1|  |  |  |  |  |  |  |  |  |  1 SMD resistor 0805 2K2 0.125W
 2|  |  |  |  |  |  |  |  |  |  |  2 Washer spring M6 x 1.9mm
  | 2|  |  |  |  |  |  |  |  |  |  2 Square button 6mm
 2|  |  |  |  |  |  |  |  |  | 2|  4 Washer star M2 x 0.3mm
 1|  |  |  |  |  |  |  |  |  |  |  1 Washer star M3 x 0.5mm
  |  |  |  |  |  |  |  |  | 1|  |  1 Threaded rod M8 x 79mm - not shown
 2|  |  |  |  |  |  |  |  |  | 2|  4 Washer  M2 x 5mm x 0.3mm
 1|  | 3| 1|  |  |  |  |  |  |  |  5 Washer  M3 x 7mm x 0.5mm
  |  | 3|  |  |  |  |  |  |  |  |  3 Washer  M5 x 10mm x 1mm

Printed:
 1|  |  |  |  |  |  |  |  |  |  |  1 base.stl
  |  | 1|  |  |  |  |  |  |  |  |  1 bracket.stl
  |  |  | 1|  |  |  |  |  |  |  |  1 cover.stl
  |  |  |  | 1|  |  |  |  |  |  |  1 idler.stl
  |  |  |  |  |  |  | 1|  |  |  |  1 pulley.stl
  |  |  |  |  |  |  |  | 1|  |  |  1 retainer.stl
  |  |  |  |  |  |  |  |  |  | 1|  1 switch_slide.stl

Assemblies:
  1 base_assembly
  1 blinder_PCB_assembly
  1 bracket_assembly
  1 cover_assembly
  1 idler_assembly
  1 main_assembly
  1 motor_assembly
  1 pulley_assembly
  1 retainer_assembly
  1 rod_assembly
  1 switch_slide_assembly

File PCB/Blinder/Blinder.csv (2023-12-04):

# | Reference | Qty | Value | Footprint | DNP
1 | C1, C3 | 2 | 100n | Capacitor_SMD:C_0805_2012Metric_Pad1.18x1.45mm_HandSolder
2 | C2 | 1 | 220n | Capacitor_SMD:C_0805_2012Metric_Pad1.18x1.45mm_HandSolder
3 | C4, C5 | 2 | 15n | Capacitor_SMD:C_0805_2012Metric_Pad1.18x1.45mm_HandSolder
4 | D1 | 1 | LED | LED_THT:LED_D3.0mm_Horizontal_O1.27mm_Z2.0mm
5 | IC1 | 1 | L6203 | L6203:MULTIWATT-11
6 | J1 | 1 | PWR | Connector_Molex:Molex_KK-254_AE-6410-02A_1x02_P2.54mm_Vertical
7 | J2 | 1 | PGM | Connector_PinHeader_2.54mm:PinHeader_1x06_P2.54mm_Vertical
8 | J3 | 1 | DOWN LIMIT | Connector_JST:JST_PH_B3B-PH-K_1x03_P2.00mm_Vertical
9 | J4 | 1 | UP LIMIT | Connector_JST:JST_PH_B3B-PH-K_1x03_P2.00mm_Vertical
10 | J5 | 1 | MOT | Connector_JST:JST_PH_B2B-PH-K_1x02_P2.00mm_Vertical
11 | R1, R2, R3, R4, R5 | 5 | 10K | Resistor_SMD:R_0805_2012Metric_Pad1.20x1.40mm_HandSolder
12 | R6 | 1 | 2K2 | Resistor_SMD:R_0805_2012Metric_Pad1.20x1.40mm_HandSolder
13 | R7, R8 | 2 | 1K | Resistor_SMD:R_0805_2012Metric_Pad1.20x1.40mm_HandSolder
14 | SW1 | 1 | UP | Button_Switch_THT:SW_Tactile_SPST_Angled_PTS645Vx39-2LFS
15 | SW2 | 1 | DOWN | Button_Switch_THT:SW_Tactile_SPST_Angled_PTS645Vx39-2LFS
16 | U1 | 1 | 3.3V | NopHead:TinyBuck
17 | U2 | 1 | ESP-12F | RF_Module:ESP-12E

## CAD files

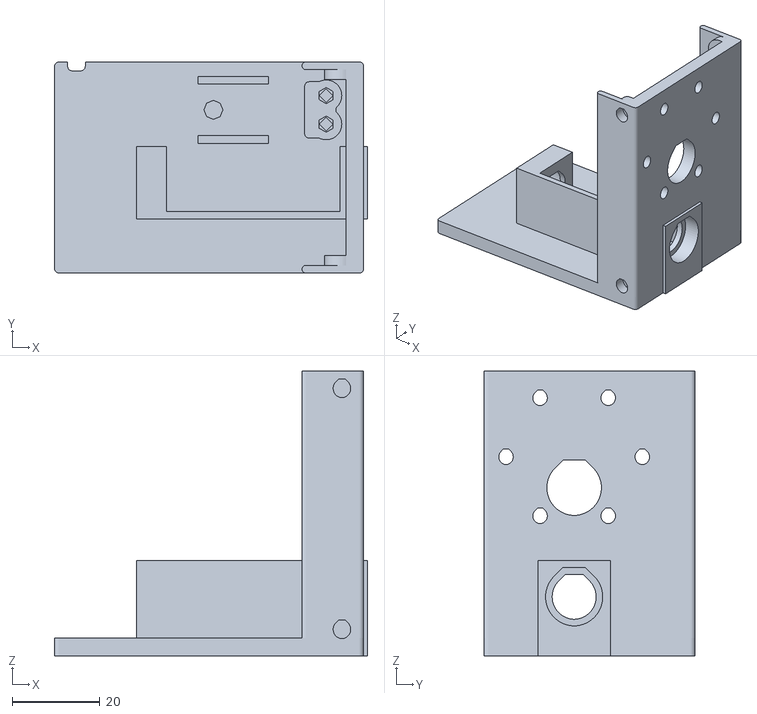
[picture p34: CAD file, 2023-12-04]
stls/base.stl
71.2 x 48.0 x 64.7

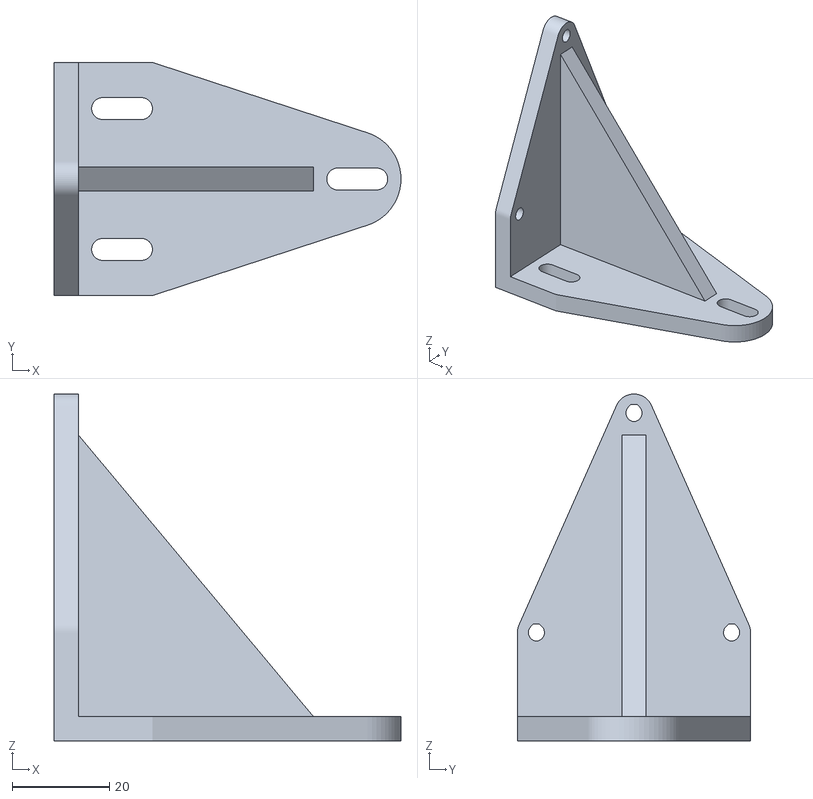
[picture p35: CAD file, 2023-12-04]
stls/printed/bracket.stl
71.4 x 48.0 x 71.4

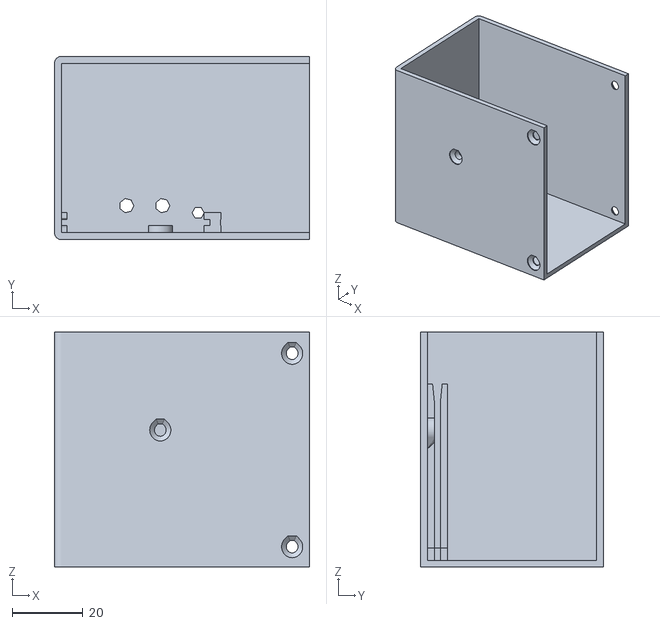
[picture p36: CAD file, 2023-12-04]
stls/printed/cover.stl
72.3 x 52.0 x 66.5

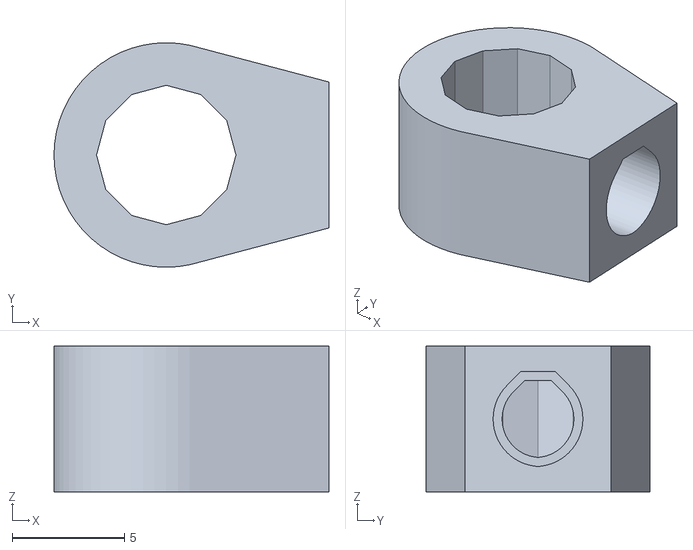
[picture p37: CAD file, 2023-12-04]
stls/retainer.stl
12.2 x 10.0 x 6.50

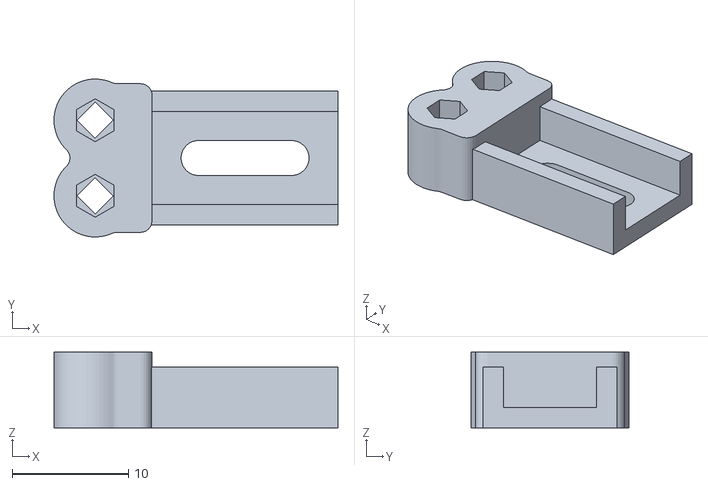
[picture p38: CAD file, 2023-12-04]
stls/switch_slide.stl
24.4 x 13.6 x 6.51

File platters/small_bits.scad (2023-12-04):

include <NopSCADlib/core.scad>

use <../scad/blinder.scad>
use <../scad/pulley.scad>


translate([-37, 0])
    switch_slide_stl();

pulley_stl();

translate([31, 0])
    idler_stl();

translate([52, 0])
    retainer_stl();

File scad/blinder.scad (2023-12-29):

//
// Blinder Copyright Chris Palmer 2023
// nop.head@gmail.com
// hydraraptor.blogspot.com
// GPL3, see COPYING
//

//!
//! Tasmota roller blind open / close mechanism
//!
$pp1_colour = grey(95);
$pp2_colour = grey(95);
$vitamin_fa = 2;
$vitamin_fs = 0.1;
include <NopSCADlib/core.scad>
include <global.scad>

use <pulley.scad>
use <NopSCADlib/utils/maths.scad>
use <NopSCADlib/utils/thread.scad>
use <NopSCADlib/utils/sector.scad>
use <NopSCADlib/utils/round.scad>
use <NopSCADlib/vitamins/insert.scad>
use <NopSCADlib/vitamins/pcb.scad>
use <NopSCADlib/vitamins/led.scad>
use <NopSCADlib/vitamins/button.scad>

include <NopSCADlib/vitamins/ball_bearings.scad>
include <NopSCADlib/vitamins/microswitches.scad>
use <pcb.scad>

switch_pos = 0; //[-1: 1]
shaft_rot = 0; // [0: 360]
show_motor = true;
show_cover = true;
show_top = true;
show_base = true;
show_pcb = true;
show_bracket = true;
motor_alpha = 1; // [0: 0.1: 1]
ymax = 1; // [-1 : 0.1 : 1]
/*[Hidden]*/

use <NopSCADlib/vitamins/rod.scad>
wall = 1.75;
side_wall = 2;

bearing = BB686;

top_clearance = max(-gm_motor_pos(motor).y + gm_motor_d(motor) / 2, gm_shaft_offset(motor).y + gm_box_width(motor) / 2) + 1;
bot_clearance = 1;
bearing_wall = wall;
axle_d = 5.98;
studding_d = 8;
nut = M8_nut;
washer = M6_washer;
microswitch = small_microswitch;
switch_size = microswitch_size(microswitch);
switch_extent = -microswitch_lower_extent(microswitch);

lever = [18 - switch_size.x / 2, 3.6, 0.5];
pivot = [-switch_size.x / 2 + 1.25, switch_size.y / 2 - 1];
op = 9.5 - switch_size.y / 2;

turns = 13;
travel = turns * metric_coarse_pitch(studding_d);
slide_slot = 8;
studding_length = ceil(switch_extent + op + nut_thickness(nut) + travel + slide_slot / 2 + op  - switch_size.y / 2);
pcb = Blinder_pcb();
pcb_cutout = 10;
pcb_z = 2;
pcb_size = pcb_size(pcb);
pcb_screw = alternate_screw(hs_cs_cap, pcb_screw(pcb));

front_t = 4;
pcb_back_from_motor = 4;
switch_back = front_t + 1 + studding_length + switch_size.y / 2 + switch_extent;
switch_top = pulley_d() / 2 + bot_clearance + switch_size.z / 2;

front_height = bot_clearance + 1.5 * pulley_d() + top_clearance;

base_length = max(front_t + gm_depth(motor) + pcb_back_from_motor, (switch_top > front_height - pcb_size.y) ? switch_back + pcb_size.x - pcb_cutout : 0);
supported_length = studding_length + 2 * bb_width(bearing);
base_width = max(gm_box(motor).x + 4, (6.75 * sqrt(gm_motor_d(motor) / 27.5) + pcb_z - gm_motor_pos(motor).x + gm_motor_d(motor) / 2 + gm_box(motor).x / 2 + 2));
base  = [base_length, base_width, 4, 1];

front = [front_t, base.y, front_height, base[3]];

shaft_pos = gm_shaft_pos(motor);

motor_pos  = [base.x / 2 - front.x, -base.y / 2 + 2 + gm_box(motor).x / 2, front.z + gm_shaft_offset(motor).y - top_clearance];
pulley_pos = motor_pos + [shaft_pos.z + shaft_l - max(shaft_l2, pulley_h()), -shaft_pos.x, -shaft_pos.y];
idler_pos  = pulley_pos - [0, 0, pulley_d()];
pcb_pos = [-base.x / 2 + pcb_size.x / 2,
           front.y / 2 - pcb_z,
           front.z - pcb_size.y / 2];

bearing_pos = idler_pos - [bb_width(bearing) /2 + spring_washer_thickness(washer), 0, 0];


studding_pos = bearing_pos - [bb_width(bearing) / 2, 0, 0];
axle_pos = studding_pos + [ceil(bb_width(bearing) + spring_washer_thickness(washer) + pulley_h()), 0, 0];

microswitch_pos = bearing_pos + [-bb_width(bearing) / 2 - switch_extent, studding_d / 2 + 1 + lever.x, 0];
microswitch2_pos = microswitch_pos  - [2 * op + nut_thickness(nut) + travel, 0, 0];

axle_length = ceil(studding_length + 2 * bb_width(bearing) + 2 * spring_washer_thickness(washer) + pulley_h() + retainer_h() + 2);
bearing2_pos = bearing_pos - [studding_length + bb_width(bearing), 0, 0];

switch_screw = find_screw(hs_cap, microswitch_hole_d(microswitch));
switch_insert = screw_insert(switch_screw);

slide_screw = M3_cap_screw;
slide_washer = screw_washer(slide_screw);
slide_insert = screw_insert(slide_screw, short = true);
channel_wall = 1.75;
channel = [slide_slot + washer_diameter(slide_washer) + 1, washer_diameter(slide_washer) + 2 * channel_wall + 1, channel_wall];

mount_screw = M3_cap_screw;
mount_insert = screw_insert(mount_screw, short = true);
mount_boss_r = insert_boss_radius(mount_insert, wall);

cover = [base.x + side_wall,
         base.y + 2 * side_wall,
         front.z + wall];

module mount_screw_positions() {
    for(side = [-1, 1])
        translate([base.x / 2 - mount_boss_r, side * (base.y / 2 - mount_boss_r)])
            vflip()
                children();

    translate([base.x / 2 - supported_length + mount_boss_r, 0])
        vflip()
            children();
}

case_screw = M3_cs_cap_screw;
case_insert = screw_insert(case_screw, short = true);
case_boss_r = insert_boss_radius(case_insert, wall);
case_boss_h = insert_hole_length(case_insert) + 1;

module case_screw_positions()
    for($y = [-1, 1], $z = [-1,1])
        translate([base.x / 2 - base[3] - case_boss_r, $y * base.y / 2, $z > 0 ? front.z - case_boss_r : base.z + insert_hole_radius(case_insert)])
            rotate([90 * $y, 0, 0])
                children();

module lever_microswitch() {
    microswitch(microswitch);

    end_pos = [lever.x, op - lever.z];
    button = microswitch_button_pos(microswitch);
    angle = atan2(end_pos.y - button.y, end_pos.x - button.x);
    length = sqrt(sqr(end_pos.y - button.y) + sqr(end_pos.x - button.x));
    dx = button.x - pivot.x - lever.z / 2;
    extension = dx / cos(angle);
    dy = extension * sin(angle);
    color(silver) {
        translate(end_pos)
            rotate(angle)
                translate([-length - extension, 0, -lever.y / 2])
                    cube([length + extension, lever.z, lever.y]);

        translate([pivot.x - lever.z / 2, pivot.y, -lever.y / 2])
            cube([lever.z, button.y - pivot.y - dy, lever.y]);

        translate([pivot.x + lever.z / 2, button.y - dy])
            linear_extrude(lever.y, center = true)
                sector(r = lever.z, start_angle = 90 + angle, end_angle = 180, $fn = fn);
    }
}

module slide_screw_pos(z = base.z)
    translate([microswitch2_pos.x + switch_size.y / 2 + channel.x / 2, microswitch2_pos.y, z])
        children();

module base_stl() {
    rib = [10 + front.x, channel_wall, front.z - base.z];

    stl("base") {
        difference() {
            union() {
                rounded_rectangle(base, base[3]);

                slide_screw_pos()
                    for(side = [-1, 1])
                        translate([channel.x / 2 - washer_radius(slide_washer), side * (channel.y + channel_wall + 0.2) / 2])
                            cube([channel.x, channel_wall, 2], center = true);

                for(side = [-1, 1])
                    translate([base.x / 2 - rib.x / 2, side * (base.y - rib.y) / 2, base.z])
                        rounded_rectangle(rib, channel_wall / 2 - eps);

                translate([base.x / 2 - front.x / 2, 0])
                    rounded_rectangle(front, front[3]);

                w = bb_diameter(bearing) + 2 * bearing_wall;
                z = bearing_pos.z - w / 2;

                translate(bearing_pos + [-bb_width(bearing) / 2 - bearing_wall, -w / 2, -bearing_pos.z])
                    cube([bearing_wall + bb_width(bearing) - 0.5, w, w + z]);

                translate(bearing2_pos + [-bb_width(bearing) / 2, -w / 2, -bearing_pos.z])
                    cube([bearing_wall + bb_width(bearing), w, w + z]);

                translate((bearing_pos + bearing2_pos) / 2 - [0, nut_flat_radius(M8_nut) + bearing_wall / 2, z / 2])
                    cube([bearing_pos.x - bearing2_pos.x,  bearing_wall, w + z], center = true);

                translate([microswitch_pos.x, microswitch_pos.y])
                    linear_extrude(microswitch_pos.z - switch_size.z / 2)
                        round(1)
                            union() {
                                square([switch_size.y, switch_size.x], center = true);

                                rotate(90)
                                    microswitch_hole_positions(microswitch)
                                        circle(insert_boss_radius(switch_insert, 1.7));
                            }
                case_screw_positions()
                    hull() {
                        h = case_boss_h;

                        cylinder(r = case_boss_r, h = h);

                        if($z > 0)
                            translate([(case_boss_r + front[3] - front.x), - (case_boss_r + h - rib.y) * $y, rib.y])
                                cube(eps);
                    }
            }


            translate(motor_pos)
                rotate([-90, 0, -90]) {
                    translate(gm_shaft_offset(motor))
                        rotate(180)
                            teardrop_plus(r = gm_boss(motor).x / 2 + 0.2, h = 100, center = true);
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

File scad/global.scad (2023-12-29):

//
// Blinder Copyright Chris Palmer 2023
// nop.head@gmail.com
// hydraraptor.blogspot.com
// GPL3, see COPYING
//
include <NopSCADlib/vitamins/gear_motors.scad>

//motor = GMAG_404327;
motor = FIT0492_A;
shaft_r = gm_shaft_r(motor);
shaft_flat_d = gm_shaft_flat_w(motor);
shaft_l = gm_shaft_length(motor);
shaft_l2 = gm_shaft_flat_l(motor);

ball_r = 4.4 / 2;

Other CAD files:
scad/pcb.scad
scad/pulley.scad

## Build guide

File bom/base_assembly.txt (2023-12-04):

base_assembly:
Vitamins:
  2 Ball bearing 686ZZ 6mm x 13mm x 5mm
  8 Heatfit insert M3 x 3mm
  2 Heatfit insert M2 x 4mm
  1 Microswitch DM1-00P-110-3
  1 Nut M8 x 6.5mm brass
  2 Screw M2 cap x 10mm
  1 Screw M3 cap x  5mm
  2 Washer spring M6 x 1.9mm
  2 Washer star M2 x 0.3mm
  1 Washer star M3 x 0.5mm
  2 Washer  M2 x 5mm x 0.3mm
  1 Washer  M3 x 7mm x 0.5mm

Printed:
  1 base.stl

Assemblies:
  1 idler_assembly
  1 retainer_assembly
  1 rod_assembly
  1 switch_slide_assembly

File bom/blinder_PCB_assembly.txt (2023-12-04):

blinder_PCB_assembly:
Vitamins:
  1 JST PH connector 2 way
  2 JST PH connector 3 way
  1 LED 3 mm green
  1 Molex KK header 2 way
  1 Molex KK housing 2 way
  1 MULTIWATT11 L6203
  1 PCB Blinder
  1 ESP-12F ESP8266 WiFi module
  1 Ultra Small 3A buck regulator
  2 SMD capacitor 0805 100n
  2 SMD capacitor 0805 15n
  1 SMD capacitor 0805 220n
  5 SMD resistor 0805 10K 0.125W
  2 SMD resistor 0805 1K 0.125W
  1 SMD resistor 0805 2K2 0.125W
  2 Square button 6mm

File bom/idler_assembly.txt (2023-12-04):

idler_assembly:
Vitamins:
  1 Heatfit insert M3 x 3mm
  1 Screw M3 grub x  5mm

Printed:
  1 idler.stl

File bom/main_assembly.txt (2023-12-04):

main_assembly:
Vitamins:
  4 Screw M3 cs cap x  5mm

Assemblies:
  1 bracket_assembly
  1 cover_assembly

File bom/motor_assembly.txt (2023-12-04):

motor_assembly:
Vitamins:
  6 Screw M3 dome x 12mm

Assemblies:
  1 base_assembly
  1 pulley_assembly

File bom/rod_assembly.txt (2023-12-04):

rod_assembly:
Vitamins:
  1 Threaded rod M8 x 79mm - not shown

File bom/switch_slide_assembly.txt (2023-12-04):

switch_slide_assembly:
Vitamins:
  2 Heatfit insert M2 x 4mm
  1 Microswitch DM1-00P-110-3
  2 Screw M2 cap x 10mm
  2 Washer star M2 x 0.3mm
  2 Washer  M2 x 5mm x 0.3mm

Printed:
  1 switch_slide.stl

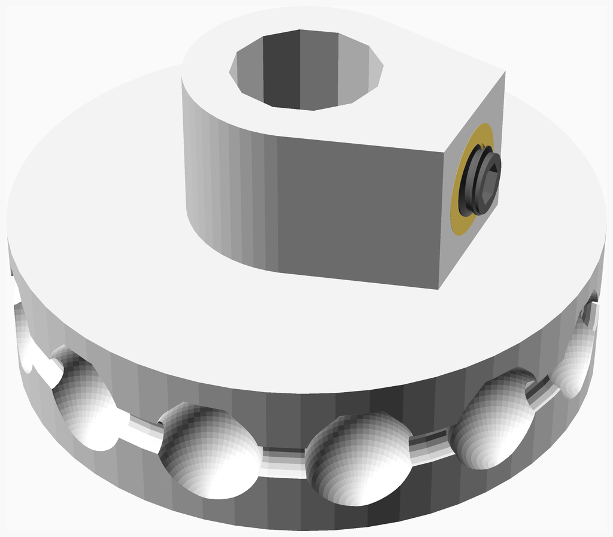
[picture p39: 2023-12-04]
assemblies/idler_assembled.png

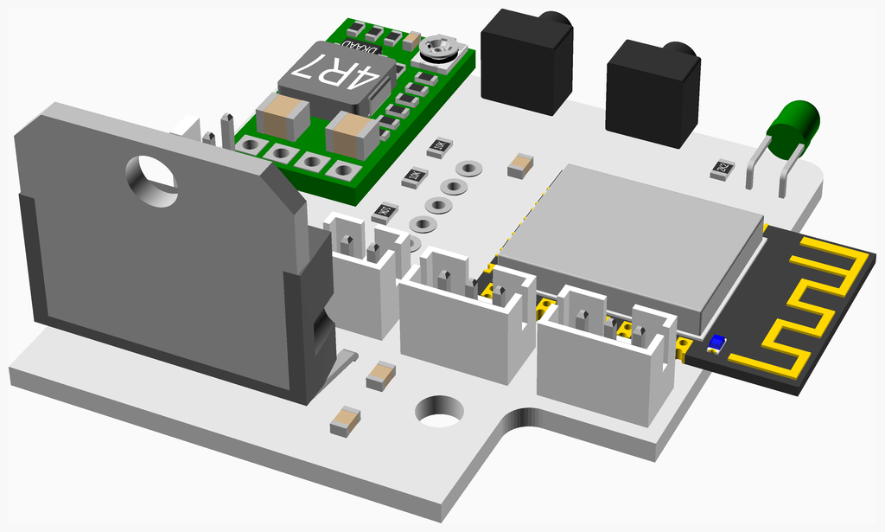
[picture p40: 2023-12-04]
assemblies/blinder_PCB_assembled.png

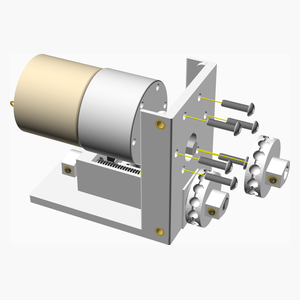
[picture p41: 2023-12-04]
assemblies/motor_assembly_tn.png

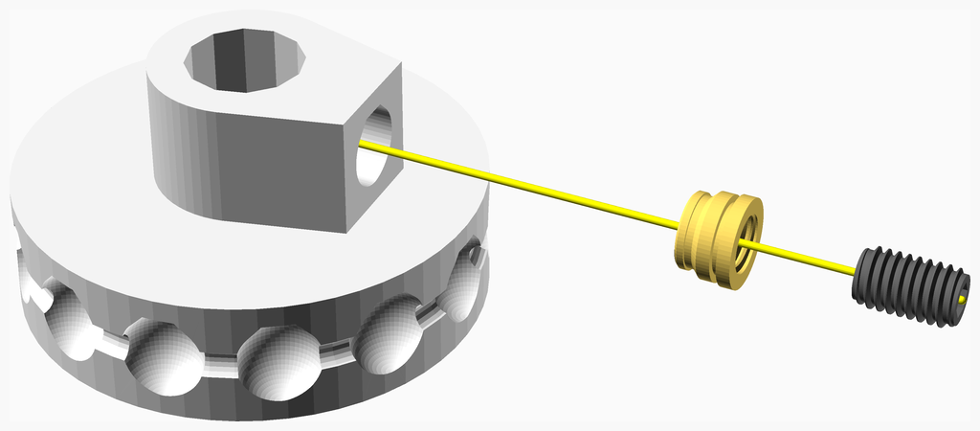
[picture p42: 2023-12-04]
assemblies/idler_assembly.png

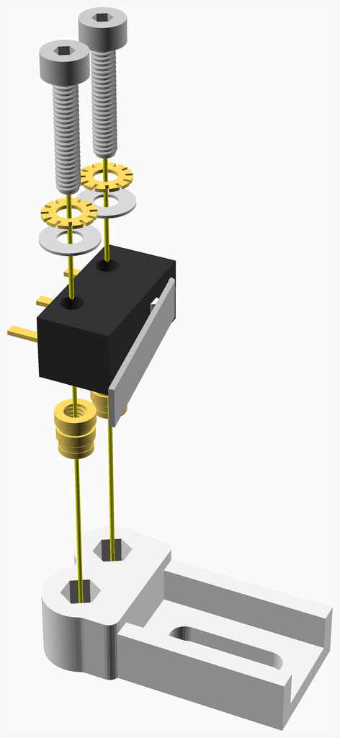
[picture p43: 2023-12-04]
assemblies/switch_slide_assembly.png

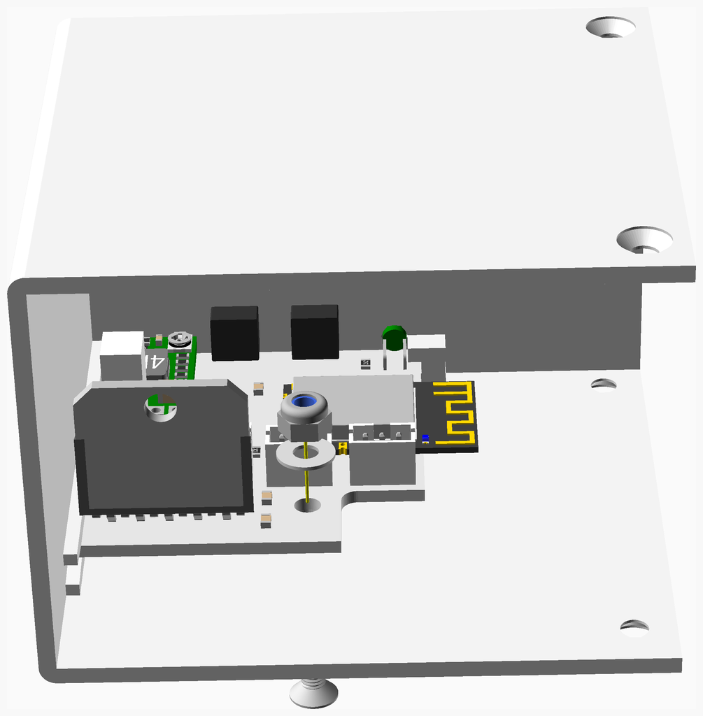
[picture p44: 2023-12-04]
assemblies/cover_assembly.png

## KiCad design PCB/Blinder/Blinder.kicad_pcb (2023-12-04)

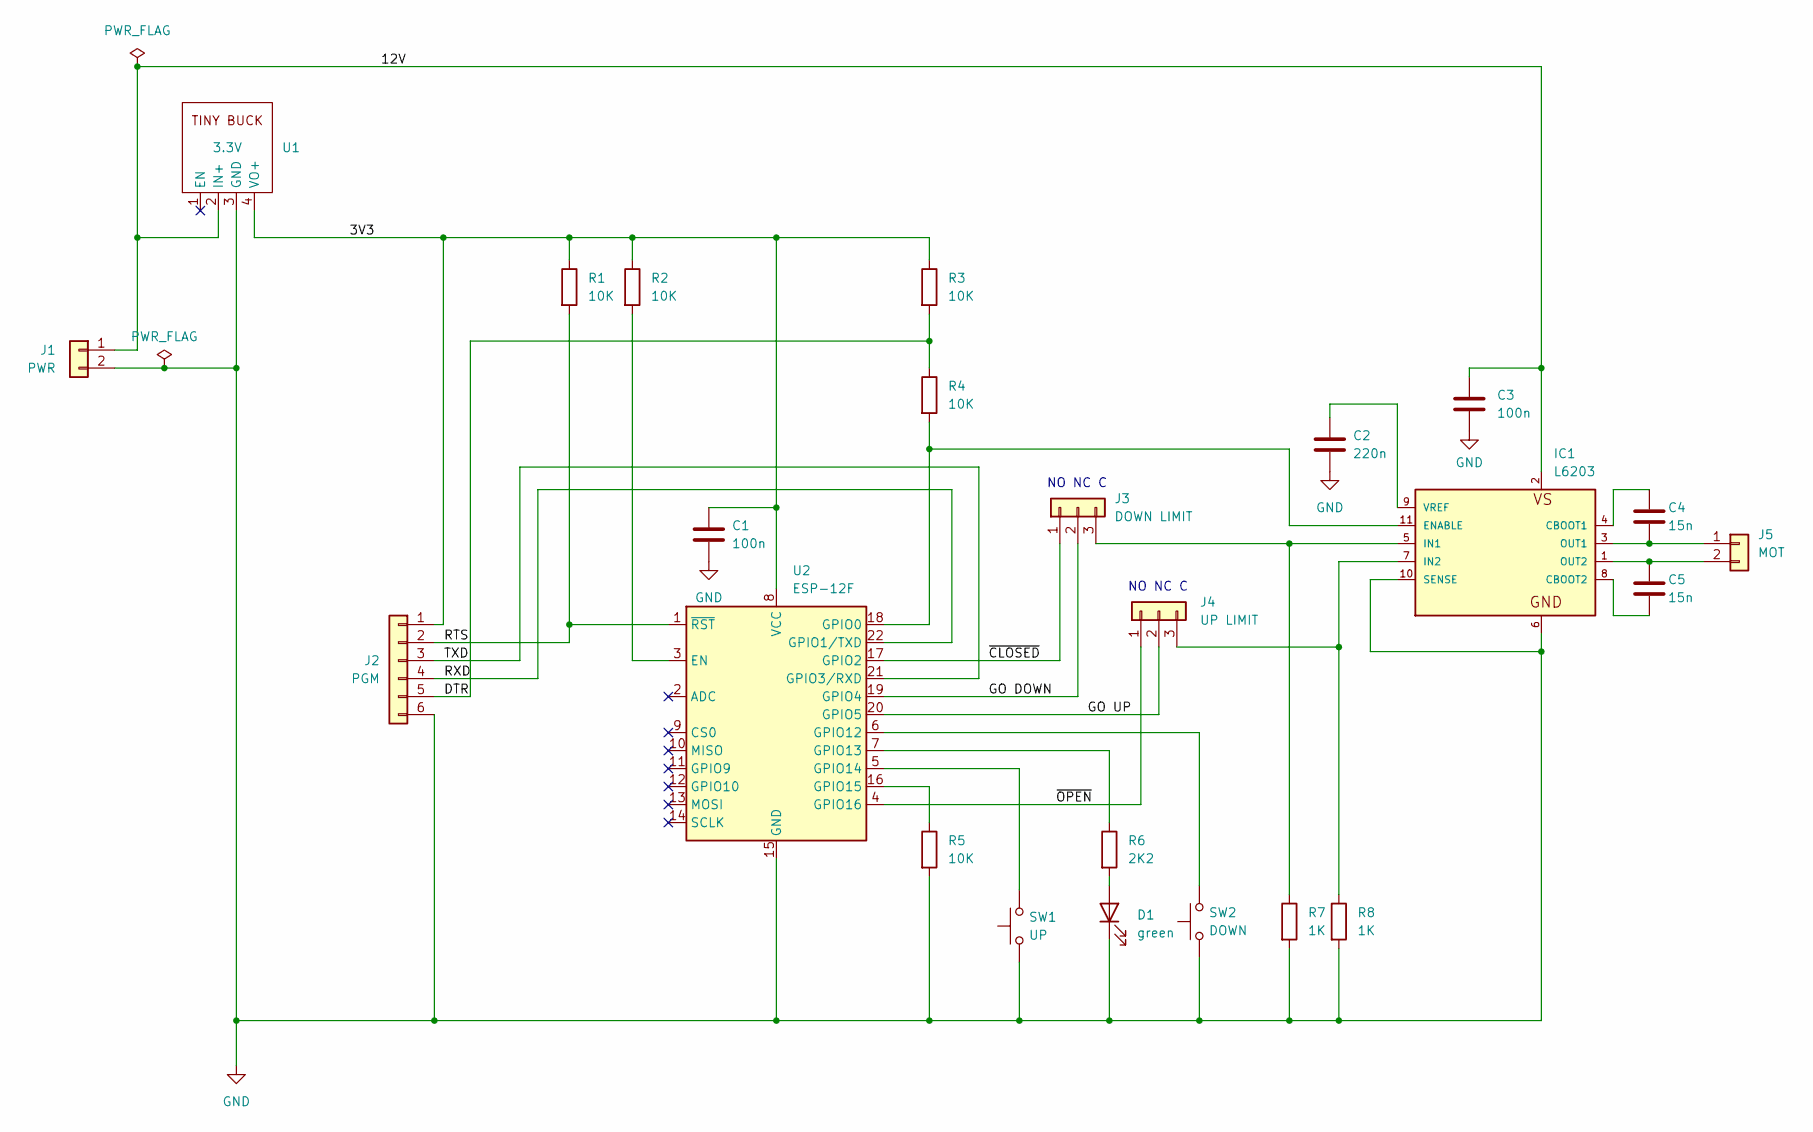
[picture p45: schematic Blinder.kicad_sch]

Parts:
C1, C3: 100n; C_0805_2012Metric_Pad1.18x1.45mm_HandSolder
C2: 220n; C_0805_2012Metric_Pad1.18x1.45mm_HandSolder
C4, C5: 15n; C_0805_2012Metric_Pad1.18x1.45mm_HandSolder
D1: green; LED_D3.0mm_Horizontal_O1.27mm_Z2.0mm
IC1: L6203; MULTIWATT-11; MPN L6203
J1: PWR; Molex_KK-254_AE-6410-02A_1x02_P2.54mm_Vertical
J2: PGM; PinHeader_1x06_P2.54mm_Vertical
J3: DOWN LIMIT; JST_PH_B3B-PH-K_1x03_P2.00mm_Vertical
J4: UP LIMIT; JST_PH_B3B-PH-K_1x03_P2.00mm_Vertical
J5: MOT; JST_PH_B2B-PH-K_1x02_P2.00mm_Vertical
R1, R2, R3, R4, R5: 10K; R_0805_2012Metric_Pad1.20x1.40mm_HandSolder
R6: 2K2; R_0805_2012Metric_Pad1.20x1.40mm_HandSolder
R7, R8: 1K; R_0805_2012Metric_Pad1.20x1.40mm_HandSolder
SW1: UP; SW_Tactile_SPST_Angled_PTS645Vx39-2LFS
SW2: DOWN; SW_Tactile_SPST_Angled_PTS645Vx39-2LFS
U1: 3.3V; TinyBuck
U2: ESP-12F; ESP-12E

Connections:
/3V3: C1.1, J2.1, R1.1, R2.1, R3.1, U1.4 (VO+), U2.8 (VCC)
/12V: C3.1, IC1.2, J1.1, U1.2 (IN+)
/DTR: J2.5, R3.2, R4.1
/GO DOWN: J3.2, U2.19 (GPIO4)
/GO UP: J4.2, U2.20 (GPIO5)
/RTS: J2.2, R1.2, U2.1 (~RST)
/RXD: J2.4, U2.22 (GPIO1/TXD)
/TXD: J2.3, U2.21 (GPIO3/RXD)
/~CLOSED: J3.1, U2.17 (GPIO2)
/~OPEN: J4.1, U2.4 (GPIO16)
GND: C1.2, C2.2, C3.2, D1.1 (K), IC1.6, IC1.10 (SENSE), J1.2, J2.6, R5.2, R7.2, R8.2, SW1.1, SW2.1, U1.3 (GND), U2.15 (GND)
unnamed: D1.2 (A), R6.2
unnamed: C4.1, IC1.4 (CBOOT1)
unnamed: C5.2, IC1.8 (CBOOT2)
unnamed: IC1.11 (ENABLE), R4.2, U2.18 (GPIO0)
unnamed: IC1.5 (IN1), J3.3, R7.1
unnamed: IC1.7 (IN2), J4.3, R8.1
unnamed: C4.2, IC1.3 (OUT1), J5.1
unnamed: C5.1, IC1.1 (OUT2), J5.2
unnamed: C2.1, IC1.9 (VREF)
unnamed: R2.2, U2.3 (EN)
unnamed: SW2.2, U2.6 (GPIO12)
unnamed: R6.1, U2.7 (GPIO13)
unnamed: SW1.2, U2.5 (GPIO14)
unnamed: R5.1, U2.16 (GPIO15)

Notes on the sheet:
NO NC C

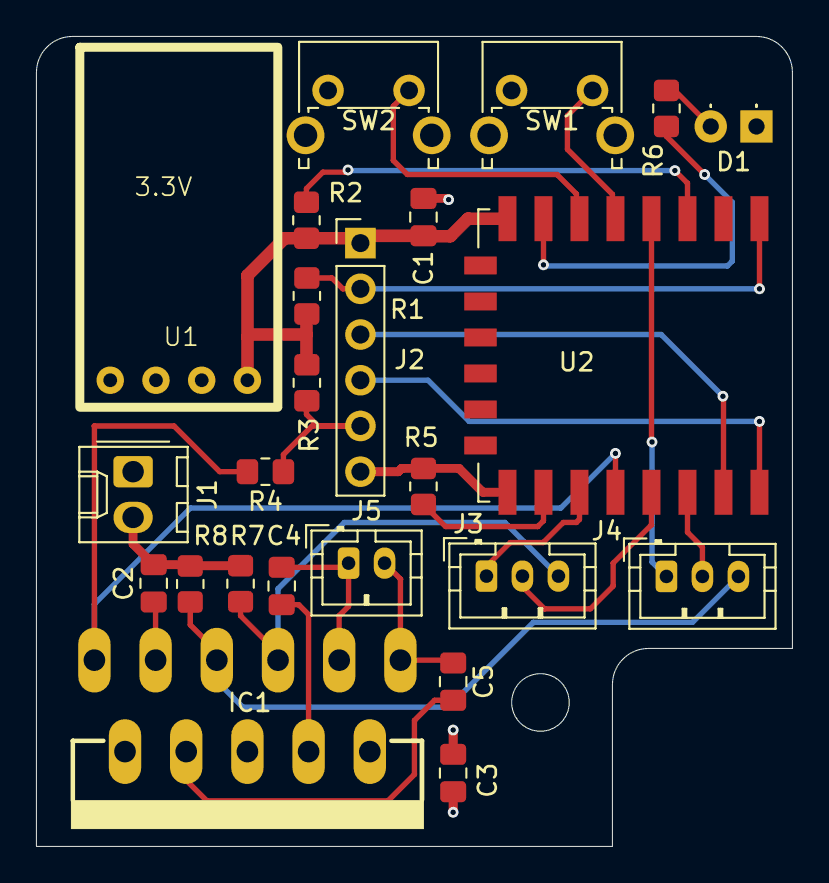
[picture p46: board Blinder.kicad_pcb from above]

Board: 4 copper layers, 42.0 x 45.0 mm, 24 parts (0 on the bottom side), 25 nets.

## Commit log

2023-12-04 First commit.
    [Blinder-B_Cu.gbr, Blinder-B_Mask.gbr, Blinder-B_Silkscreen.gbr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]
2023-12-04 Fixed parts list width.
    [pulley.scad]
2023-12-29 Fixed copywrite dates.
    [blinder.scad, global.scad, pcb.scad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]
